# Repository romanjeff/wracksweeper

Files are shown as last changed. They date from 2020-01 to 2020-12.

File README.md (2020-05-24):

We are a Capstone team working with the Portland State University NEAR lab, under advisement by Dr. Martin
Siderius, and this repo is for the necessary files to implement or reference tha customizations we have done
to the AUV owned by the NEAR lab for academic research purposes. 

Our AUV is a Riptide Systems MP1 Mk.II, managed by a Beaglebone Black running MOOS-IvP (http://www.moos-ivp.org).

The project goal is to have full side-scan sonar capabilities, an emergency asset recovery tracking beacon, 
rechargeable power supply, and long-range wireless communications allowing us to check on the AUV's status,
give it new mission parameters, or toggle sonar functions without recovery and relaunch. Added features are
modular and removable to restore original state to the AUV.

Our sonar system is an Imagenex OEM side-scan module, and our wireless communications are done over LoRa at 
915 MHz using the Adafruit Feather M0 with HopeRF RFM95 transceiver modules. 

This project has been conducted at Portland State University by a team consisting of:

Drew Wendebrn, Matthew Moore, Patrick Hawn - Mechanical Engineering.  

Roman Minko, Adel Alkharraz - Sonar Interface Software.  

Colton Bruce - Beacon and RF link characterization.  

Jeff Roman - Communications Software.  

Jens Evens, Grace Semerdjian - Power System.  

http://www.wracksweeper.com

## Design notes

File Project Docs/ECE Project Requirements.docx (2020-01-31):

Wracksweeper: Project Design Specification

Capstone Team 3, Integrating A Side Scan Sonar System Into An AUV

Industry Sponsor: Maritime Archaeological Society

Faculty Adviser: Dr. Martin Siderius

Background:

The Maritime Archaeological Society (MAS) is searching for a Spanish galleon, the Santo Christo de Burgos, which wrecked on the Oregon coast in 1693. Hundreds of artifacts including porcelain, beeswax, and teak timbers have been found on a section of shoreline. Over the past 10 years, MAS has been conducting sonar, magnetometer and diving searches for the wreck. The searches have been severely limited due to difficult ocean surface conditions in the search area. The small boats used for the surveys and dives must launch at very precise tide levels to access the site which is a 45 minute boat ride away. Once on site, rough seas and submerged rocks make the operations difficult and potentially dangerous to the crew.

Problem:

How can we conduct long duration side scan sonar surveys without tide limitations and without putting human crewmembers in potential danger?

Objective:

To facilitate the Maritime Archaeological Society’s search for the remains, it is necessary to outfit an unmanned underwater vehicle (UUV) owned by Portland State University’s NEAR lab with side-scan sonar, a rechargeable battery solution able to support at least 8 hours continuous operation, and sufficient (at least one) emergency location systems that a recovery team can track and rescue the vehicle in the event of mission failure. While the current mission is helping the Maritime Archeological Society, all upgrades to the system will be funded by the NEAR lab and the upgrades will benefit them for future research conducted with the UUV. To do this, a multi-disciplinary team consisting of Mechanical, Electrical, and Computer Engineers must specify and implement these systems. This principal objective can be subdivided into distinct subsystems which successfully achieved will in total comprise a successful solution: emergency location systems, side-scan sonar systems, power systems, and logistics systems. If the additional engineering resources exist, an additional wireless communications subsystem may be added to this roadmap.

Constraints:

For this project, all functions must be integrated onto the NEAR lab’s Riptide Systems UUV. New features must not in any way compromise the existing functionality of the UUV and must be removable to restore the UUV to its initial state. Payload components must fit within a bay 25.5” long with an internal diameter of 6.375”. The budgetary constraint is roughly $10,000, with changes to this conditional to the research value that can be added to the NEAR lab’s resources. Based on budget and project needs, we must design this system to use the already-purchased Imagenex OEM Ethernet Sidescan Sonar PCB kit, which expects sonar images to be obtained as .872 files using the Imagenex proprietary Windows-based software. This sonar system will require a computer capable of running that software, ethernet communication with the sonar, and a source capable of providing up to 2.5W power at between 22 and 33 VDC. Sonar imaging capabilities will be constrained by those of the Imagenex product, which allows imaging range scales from 10m to 200m and can provide transducer beam widths as narrow as 0.7 ° x30 ° at 800 kHz and as wide as 2.2 ° x75 ° at 260 kHz.

Requirements:

We have identified three tiers of project requirements; the must category is the minimum viable product necessary to achieve the basic objective, while the should category describes improvements which could benefit this specific project in a meaningful way and the may category describes features which allow the work of this project to be extensible to future research purposes. Though the objective is ultimately to find the shipwreck, a successful capstone completion does not require this; the successful additions of the necessary functionality to the UUV to enable finding the shipwreck shall be sufficient.

Emergency Location Services:

- We must integrate at least one functioning emergency beacon for locating the vehicle with sufficient location resolution to be tracked within 20m anywhere within 3km of shore.
- The emergency beacon should operate regardless of whether the UUV’s piloting computer is operational and remain always-on during any deployment situation.
- The emergency beacon may broadcast to worldwide networks, an FCC-regulated amateur radio band, or to marine specific tracking networks.
- We may install an acoustic transducer for underwater chirps to have extra redundancy for the emergency locator functions.

Side-Scan Sonar:

- We must implement functioning sidescan sonar capabilities onto the provided vehicle, with data preserved in a manner conducive to image analysis and exact location discovery.
- We must provide the means to correlate sonar imaging to geographic location based on predicted GPS coordinates.
- We must provide a payload computer capable of controlling the sonar hardware either through the provided Windows-based software or code of our creation.
- We must furnish the sonar system with enough memory to store full missions at the maximum (10m image distance) rate of 265MB/hr of data collection, meaning a minimum of at least 3GB dedicated memory just for sonar data to store one mission and account a memory guardband.
- The memory device should be one which is resistant to turbulence and motion-induced write or read errors, such as a solid state drive or USB flash drive.
- We should have enough available memory for at least 10 missions to reduce the need to clear memory before each deployment.

Logistics/Power:

- We must achieve consistently predictable mission behavior and a general piloting guideline for the vehicle, which has not yet been exhaustively tested by the NEAR lab. This will be manifested as design documentation and operating manual for all integrated components.
- We must implement a battery solution for the emergency location system(s) with at least one month of standby time.
- We must implement a rechargeable battery solution with at least 1400 Watt-hours (the nominal value of the current C-cell alkaline battery pack).
- The battery pack should offer enough power for at least 8 hours’ system operation at full system load.
- The battery pack must have a charging mechanism capable of charging the full pack in less than 24 hours.
- The battery pack must be rated to at least 200 full charge/discharge cycles.
- The charging mechanism should be current and voltage-adjustable.
- The charging mechanism may have a quick-charge feature at higher current supply.
- We may implement the new features in a way that all created deliverables are easily swappable onto the NEAR lab’s other UUV, which is a smaller vessel.

Optional Communications Subsystem:

- We may implement a wireless communications solution on the vehicle capable of longer-distance mission updates than the WiFi communications already onboard, for location requests and/or remote updates to mission parameters from distances greater than 75 feet. .
- We may implement this system with sufficiently high datarate to allow remote download of sonar files without AUV recovery for redeployment after image review.

Project Requirements Capstone Team 3 Rev 2, 1/8/19 Authors: Roman, Semerjian

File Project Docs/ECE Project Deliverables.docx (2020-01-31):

Wracksweeper: ECE Subteam Milestones and Deliverables

Capstone Team 3, AUV

Sponsor: Maritime Archaeological Society

Adviser: Dr. Martin Siderius

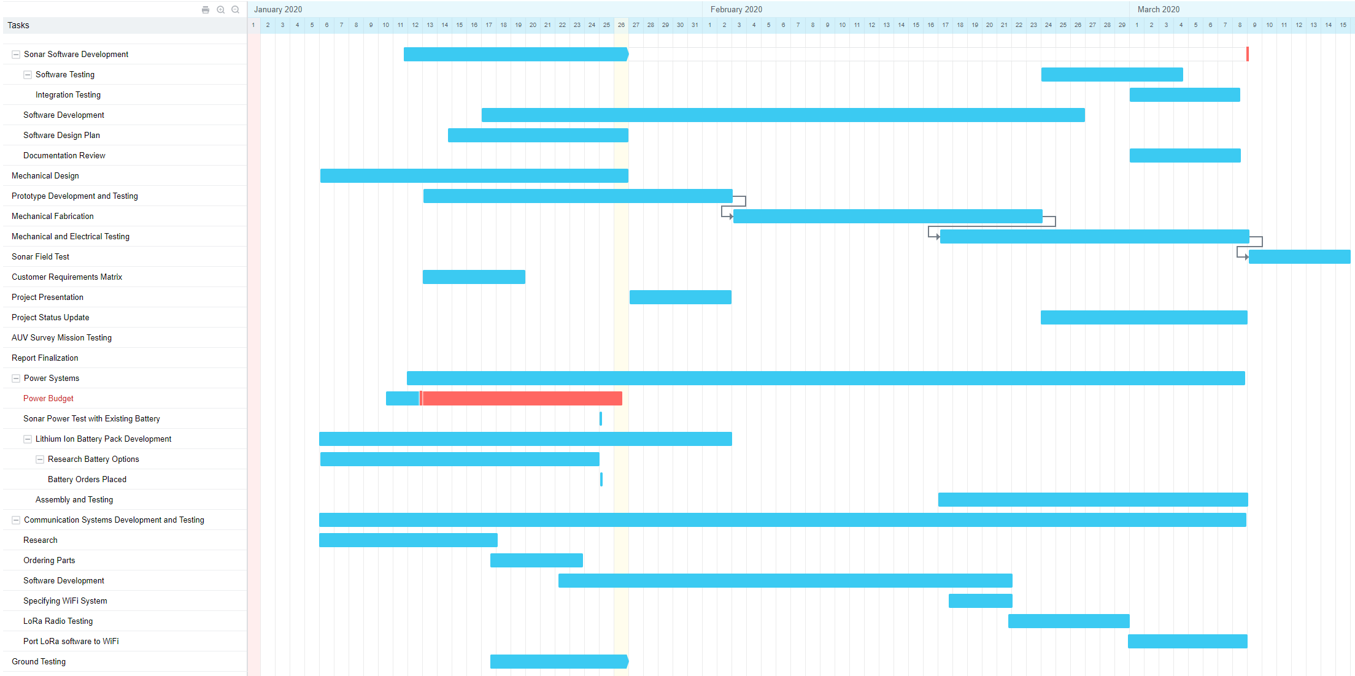
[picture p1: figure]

Figure 1: Gantt chart for the Spring term portion of the project

Key Milestones

I. Create product design specification.
II. Build project schedule.
III. Present project proposal to industry sponsor
IV. Present final project to industry sponsor and faculty adviser
V. Specification milestones:
  A. Specify power module hardware
  B. Specify sonar integration software
  C. Specify emergency location services hardware
  D. Specify remote communications hardware
VI. Modular Test Milestones
  A. Successfully test power system
  B. Successful hardware integration of power system
  C. Successfully test sonar hardware
  D. Successfully test sonar software
  E. Successful hardware integration of sonar
  F. Successfully test emergency location hardware
  G. Successful hardware integration of emergency location
  H. Successfully test remote communications hardware
  I. Successfully test remote communications software
  J. Successful hardware integration of remote communications
VII. Integration Milestones
  A. Successful systems integration test (done on dry land)
    1. Create and store sonar images physically onto IC
    2. Get location from beacon
    3. Request and receive location from AUV using wireless communications, possibly update MOOS mission and/or retrieve sonar image data
    4. Recharge battery
VIII. Performance Test Milestones
A. Characterize battery life
  a. Characterize voltage regulation and boost voltage
B. Characterize sonar performance.
C. Characterize location accuracy of emergency locations hardware
D. Characterize remote communications datarate and range.
E. Successful test mission demonstrating full system operation in water
  a. Potentially: ocean-based demonstration mission to characterize ocean performance of system

Key Deliverables

I. Product Design Specification
II. Project Schedule
III. Software to run sidescan sonar on Linux-based computer
IV. Software to allow remote user control of MOOS and possibly sonar using wireless communications.
V. AUV new features
  A. Side-scan sonar
  B. Rechargeable Battery System
  C. Asset tracking system
  D. Wireless communications system
VI. Documentation
  A. Software documented sufficiently to allow new users to install, use, and possibly adapt any code
  B. “Piloting” guide to AUV to simplify the process of generating mission parameters for MOOS-IvP
  C. Written report describing full scope of project including data
  D. Datasheets for all added components.
  E. Full revision history of all code
  F. Recorded minutes from weekly meetings documenting project progress over time.
  G. System block diagram that details the full system and differentiates between legacy hardware and new additions done by the capstone team

ECE Project Milestones and Deliverables Capstone Team 3 Rev 1, 1/29/19 Authors: Roman, Wendeborn, Semerjian

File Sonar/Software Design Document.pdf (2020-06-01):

Software Design Document | Wracksweeper (Capstone Team
3)
Version 1.1 (1/31/2020) | Authors: Roman Minko, Adel Alkharraz

Software Requirements:
Must:
- Have communication between the payload computer and the sonar board through ethernet.
- Keep writing data at every ping to the .872 file and return the file.
- Allow the sonar board to accept up to 27 bytes of switch data from the payload computer.
- Be able to start/stop recording data from MOOS.
- Be able to communicate data from the payload computer to the main computer through USB to Ethernet through a dongle.
Should:
- Implement GPS/NAV MOOS variables in the .872 file.
- Have an on/off status to MOOS whether or not the sonar system is on or off.
- Control the inputs of range, mode/frequency, gain, and balance gain.
May:
- Implement the altimeter MOOS variable in the .872 file.
- Create a script to run the program at a certain depth and stop running the program at a certain depth.

Technology Needed:
Language:
- C++
Framework:
- MOOS IVP
Network:
- TCP/IP
Source Control:
- Github

Version 1.1 (1/31/2020) | Authors: Roman Minko, Adel Alkharraz

Program Algorithm:
1. Program socket clients and check ethernet connection between the sonar board and the payload computer.
2. Create an empty .872 file that will generate data to be stored for each ping.
3. Create an array of strings that will store 27 bytes of switch data and will be passed from the PC to the sonar system.
4. Set up USB to Ethernet communication protocol between both computers.
5. Set fixed values for array:
- Byte 0 (Switch Data Header) = 0xFE
- Byte 1 (Switch Data Header) = 0x44
- Byte 2 (Reserved) = 0x00
- Bytes 4-6 (Reserved) = 0x00
- Bytes 9-17 (Reserved) = 0x00
- Byte 18 (TCP Packet Number) = 0x00 or 0x02 (will be switching on every ping)
- Bytes 19-25 (Reserved) = 0x00
- Byte 26 (Termination Byte) = 0xFD
6. Set values input from user for array:
- Byte 3 (Range) = 0x0A - 0x32 (10-50)
- Byte 7 (Frequency) = 0 - 2
- Byte 8 (Start Gain) = 0 - 40dB
7. Create a ping function that will write data to the .872 and then append that data for every new ping.
8. Receive GPS data from the pNAV application and write to the .872 file while each ping data is being processed.

Version 1.1 (1/31/2020) | Authors: Roman Minko, Adel Alkharraz

Data Flow Diagram:

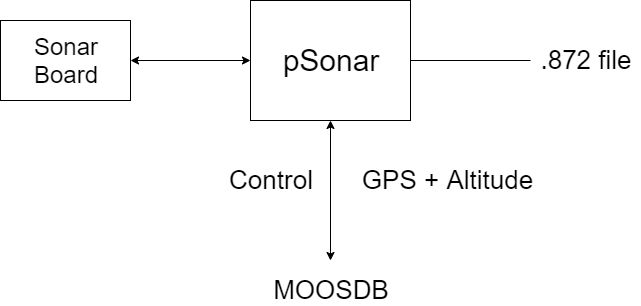
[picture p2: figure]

Hardware Diagram:

Version 1.1 (1/31/2020) | Authors: Roman Minko, Adel Alkharraz

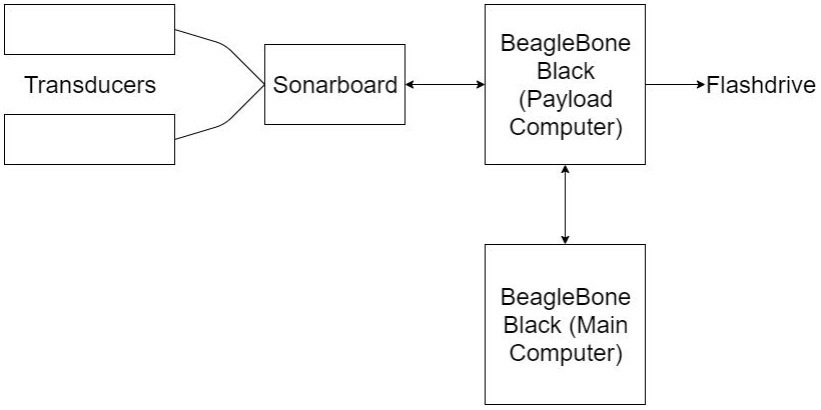
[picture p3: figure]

.872 File Reference:

Imagenex Technology Corp. "DATA STORAGE FILE FORMAT (.872)." MODEL 872 SIDESCAN (YellowFin), 1.01, Imagenex Technology, pp. 54-57. Google Drive, drive.google.com/open?id=0B4CkagcY3pD7Zmx1dFVTdnBydmdYejBQb2ZEUW5pRE tudVBR.

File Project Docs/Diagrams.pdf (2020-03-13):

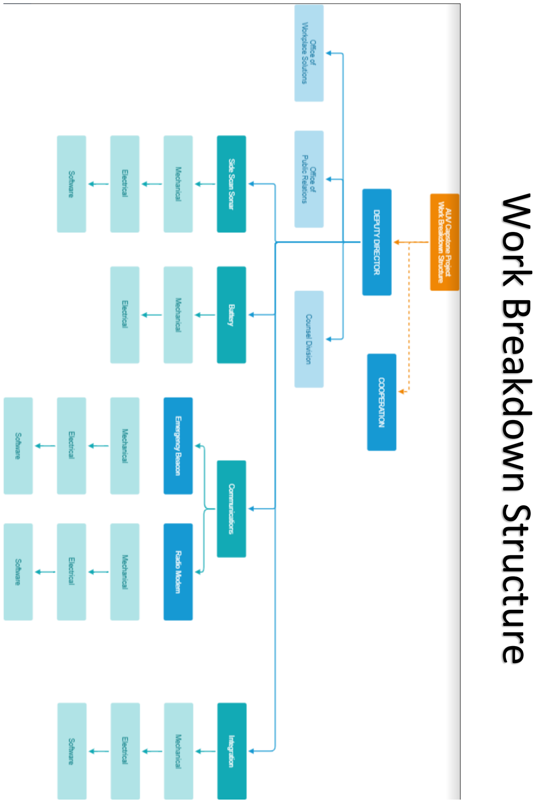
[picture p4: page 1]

Work Breakdown Structure

System Block Diagram

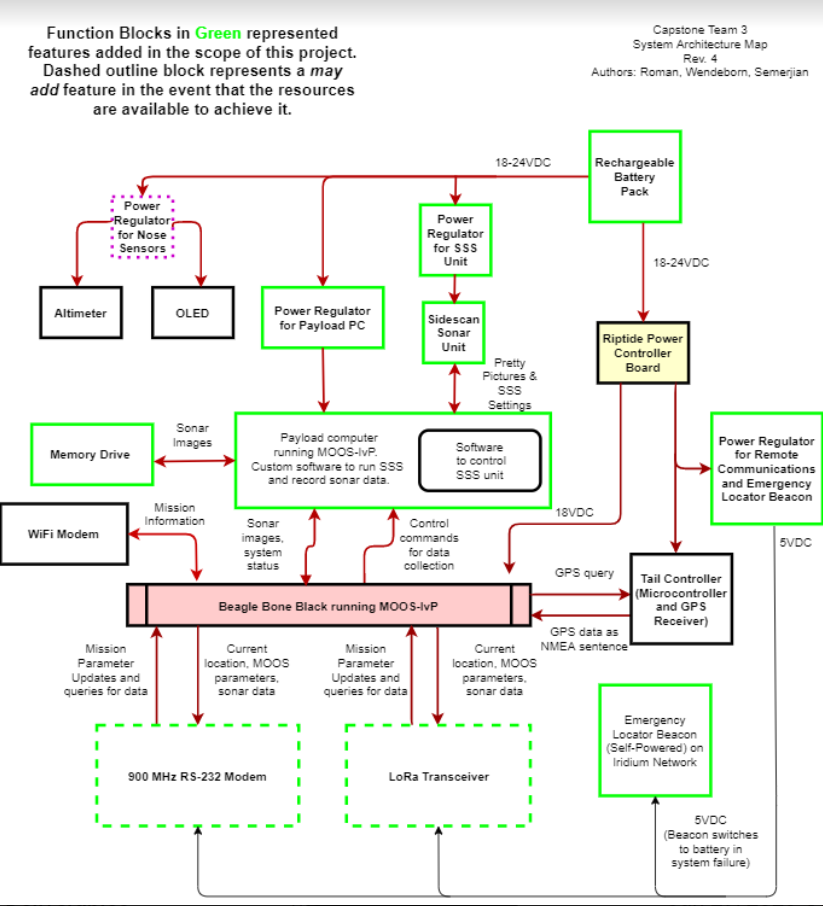
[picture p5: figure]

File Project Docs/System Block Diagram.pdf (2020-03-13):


Work Breakdown Structure

System Block Diagram


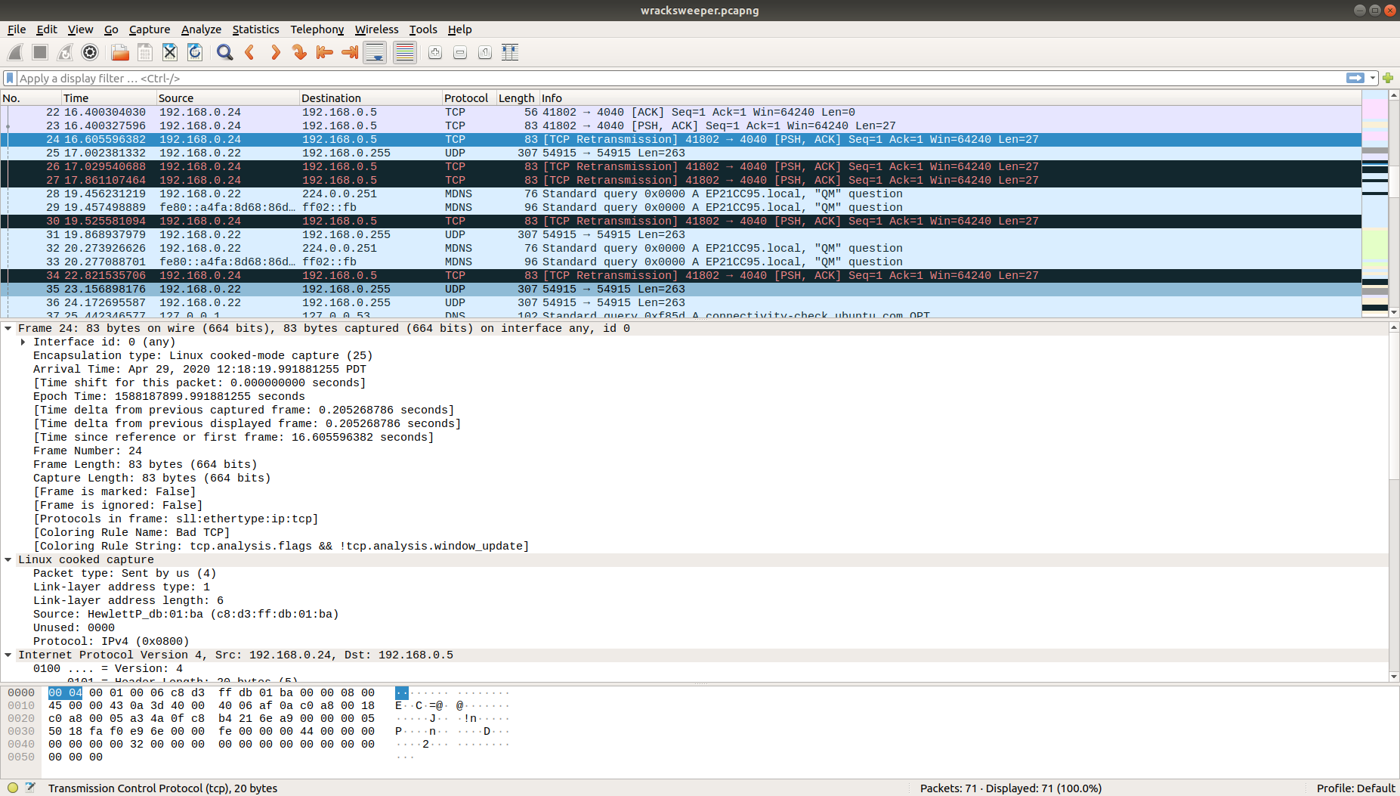
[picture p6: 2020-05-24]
Sonar/wireshark/Linux Packet Capture.png

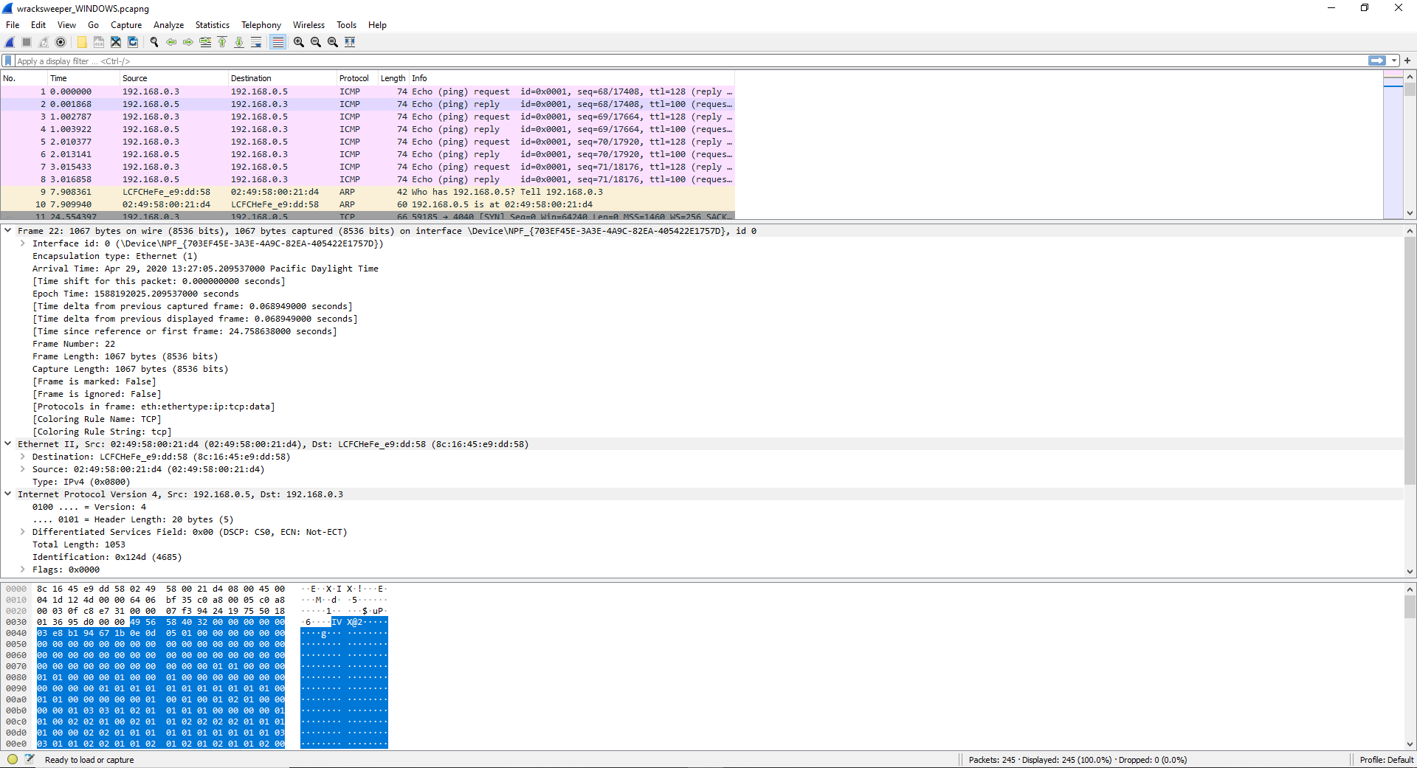
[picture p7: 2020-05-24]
Sonar/wireshark/Windows Packet Capture.PNG

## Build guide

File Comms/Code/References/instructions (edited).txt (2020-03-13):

pip3 install RPi.GPIO
pip3 install spidev
pip3 install pyLoRa
sudo apt-get install python-rpi.gpio python3-rpi.gpio
sudo apt-get install python-spidev python3-spidev
sudo apt-get install git
sudo git clone https://github.com/rpsreal/pySX127x
sudo apt autoremove

Pinout
********************************
MOSI	GPIO 10
MISO	GPIO 9
SCLK	GPIO 11 
CS	GPIO 7
DIO0	GPIO 4
DIO1	GPIO 17
DIO2	GPIO 18
DIO3	GPIO 27
RST	GPIO 22
*LED	GPIO 13	(not actually being used)
********************************
++++++++++++++++++++++++++++++++++++++++++++++++++++++++++++++++++++++++++++
To find IP address for SSH:
open command line (Ctrl+Alt+t)
type in ifconfig

for WIFI:
	look at wlan0:
			inet 192.168.xx.xxx	<-- this is the ip for ssh
for Ethernet:
	look at eth0:
			inet 192.168.xx.xxx	<-- this is the ip for ssh
++++++++++++++++++++++++++++++++++++++++++++++++++++++++++++++++++++++++++++
----------------------------------------------------------------------------
To run a single easy command to SM sensor:
	-open command line (Ctrl+Alt+t)
	-cd to:
		Desktop/AirSciences/SMsensor/
	 or
		home/pi/
		(by default should be here when you open command line)
	-type command: make bang
To run a specific command to specific device:
	-open command line (Ctrl+Alt+t)
	-type command: python3 /home/pi/Desktop/AirSciences/SMsensor/LORA_PI_TX.py [SensorName]
		e.g.   python3 /home/pi/Desktop/AirSciences/SMsensor/LORA_PI_TX.py SM01

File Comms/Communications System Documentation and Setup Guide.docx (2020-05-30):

Guide to Setup and Use the WAVES Wireless Communication Subsystem

Installing and Configuring the Adafruit Feather M0 with LoRa

Both the AUV and shore controller radios use the same Arduino sketch, and both will need u.FL connectors for their antennas soldered to them in the appropriate footprint. The radio to be used in the AUV will additionally need two 2.2k resistors soldered directly: one from pin USB to A2, and one from A2 to GND. There will also be wires from GND, Tx1 and Rx0 to the Beaglebone black that need soldering. Please consult the full system wiring diagram to ensure this is correctly executed, as inverted UART connections will lead to nonfunctional communications.

(This is essentially a summary of the instructions available from Adafruit here: https://learn.adafruit.com/adafruit-feather-m0-radio-with-lora-radio-module/setup)

In order to program the Adafruit Feather M0 using the Arduino IDE, one first needs the Arduino IDE. Once the most updated version is installed, go to File->Preferences and add to the “Additional Boards Manager URL” this address:

https://adafruit.github.io/arduino-board-index/package_adafruit_index.json

If other URLs are already listed, simply add a comma and then the above (as with PATH additions).

Next, go to Tools->Boards->Board Manager and select from the “Source” dropdown menu the “Contributed” section and install the “Adafruit SAMD Boards” and “Adafruit AVR Boards” and “Arduino Leonardo and Micro MIDI-USB” libraries. Make sure to FIRST install any Arduino Boards library which has inclusions for the Feather (Arduino SAMD and Arduino AVR). Restart the IDE, then plug in the Feather M0 and verify that the Tools->Ports Menu shows “COMxx: Adafruit Feather M0” for xx whichever USB port you are plugged into. Select the correct board from Tools->Boards. Now, you can install a sketch onto the Feather! There is a sample Tx sketch and a sample Rx sketch on the Adafruit guide above which can be monitored from the Arduino serial monitor to verify that the two boards are pinging each other. DO NOT TRY TO USE THE RADIOS WITHOUT ANTENNAS. Either use a 13cm wire or your intended antenna.

The first lines of code below the library imports on the AUV_Comms Arduino sketch allow the toggling of modes. The appropriate version of the sketch is obtained by compiling and uploading after ensuring the proper toggles are either uncommented or left commented out. A guide to these possible settings is as follows:

#define SHORE_CLIENT | #define DEBUG | USE CASE

commented | commented | Official AUV installation with BBB. All arduino interaction will be over UART with no extra information or added UX dialogue. Validate both radios operational with DEBUG modes and USB terminal before switching to this setting.
uncommented | commented | Not a useful state. Avoid.
commented | uncommented | Troubleshooting AUV radio via USB with similar terminal interface as used for Shore controller radio.
uncommented | uncommented | Official shore controller radio setting. Use with USB serial interface.

Available Radio Methods:

The serial input is fairly reliable and allows backspace, so it should be fairly easy to interact with. Whatever you type will, as long as the transmission executes properly and is received and acknowledged, be relayed verbatim to the AUV Beaglebone Black from the perspective of root kernel access. This link is not suitable for interactive programs or lengthy output, and not all command line operations will behave predictably, but most may be performed by preceding your command with “sudo sh -c” to spawn a child shell from which to execute your desired operation.

The following special commands do not result in AUV interaction but govern various available radio options:

“-changemode bw500cr45 sf128” gives the syntax form for a coordinated and handshaked settings change on both radios. All settings options must be specified, with the options listed and explaiend in the next section.

“-changeme bw500cr45 sf128” allows a local-only settings change. In the event that the shore radio loses power or is reset, the same settings can be implemented to regain the link, but there is user responsibility to remember the settings they were using. Once a preferred setting is found for a specific mission’s operating territory and link conditions, it is recommended to recompile and reupload the sketches with those settings as default.

“-verb” gives verbose output to monitor link conditions, appends all received messages with total packet time from sending to receiving acknowledgement and the SNR and RSSI detected. If packet times far exceed those expected for the settings in use, it may be assumed that some retries were necessary.

“-memmon” can be used in sketch modification to check memory use over time when new features are added. If the new features cause memory leak, this may be determined by invoking this method and observing memory use changes over the course of an interaction section.

“PING” is a simple ping to test that 2-way communication is working without any AUV interactions. The response comes from the Arduino, not the BBB, and it can be convenient to check the link by turning -verb on before a ping, then turning -verb back off.

Choosing Radio Settings

The “Different LoRa Settings” Spreadsheet gives a rough guide to the datarate differences between the different available settings. Here are the meanings of those settings.

We have provided access to three of the available chirp bandwidths: 125kHz, 250kHz, and 500kHz. The smallest bandwidth is thought to offer roughly 6dB improvement in link budget (theoretically a doubling of range) but with proportionally longer packet time, about 4x greater on-air time in tests.

The coding rate sets the Hamming Code depth, from 4/5 to 4/8. The 4/5 setting only enables a single parity bit, while the 4/8 setting can detect multiple bit error locations. This setting is exclusively related to reliability and does not affect link budget, but on-air time increases slightly. This option is somewhat redundant due to the reliable datagram’s CRC and so it will not dramatically improve performance nor will it significantly hurt on-air time. It is recommended to leave at 4/5 except in specific instances.

The spreading factor specifies chips/symbol, where symbol rate is set by adjusting the number of phase changes (chips) used for each symbol. A high spreading factor results in greater on-air time but improved detection and decoding. Each increase in spreading factor doubles the on-air time but can potentially provide around 2dB improvement in link budget. The available spreading factor options are 128,256,512,1024,2048,and 4096. It is recommended to limit spreading factor to 2048 at most, as 4096 can lead to packet times up to 8s and it is likely that they will time out. The timeout setting can be adjusted in the sketch, but failed packets at faster datarate are also subject to it.

Current Default settings in the sketch:

BW: 500

CR: 4/5

SF: 256

# RETRIES: 3

TIMEOUT: 4 seconds

Each retry attempt is given the full timeout period if no acknowledge is received. This means packet failure can be detected for certain within 16 seconds of initial transmission.

Recommended default settings for poor link environments:

BW: 500

CR: 4/5

SF: 2048-4096

Estimated Packet time: 0.7-1.2s

Since the AUV is floating, it is as likely that the RF link is broken mid-packet as not and so the lowest possible spreading factor will yield best performance due to the low on-air time. However, physical link budget is 6dB worse at the higher bandwidth, which makes it something of a runoff between the following set of settings as far as possible range is concerned.

BW: 125

CR: 4/5

SF: 512 - 2048

Estimated packet time: 0.8-2.7s

Installing the Communications Software on the Beaglebone Black

1. (If starting with new Beaglebone Black) :

Flash a Debian 9.5 or earlier image onto BBB:

Create uuuv user with “sudo adduser uuuv” then make a superuser with “sudo usermod -aG sudo uuuv”. Check that it worked by “su -uuuv” then run “sudo whoami” and make sure root shows up. Unzip riptide installer package to some directory, then run ras-uuuv-dashboard-psreinstall.sh and finally install.sh, selecting 1MP, Mk. 2, Sparton IMU as the install options.

2. Log in, then:

sudo nano /etc/network/interfaces

Append to end of doc:

iface usb0 inet static

address 192.168.7.2

netmask 255.255.255.252

network 192.168.7.0

gateway 192.168.7.1

dns-nameservers 8.8.8.8

post-up route add default gw 192.168.7.1

In terminal again:

sudo reboot

Share your internet connection from “networks and sharing” in your OS, then ssh into the BBB which should now be internet-enabled to get more software up on that thing.

Once rebooted:

sudo ntpdate pool.ntp.org

sudo apt-get update

sudo apt-get install minicom build-essential python-dev python-pip -y

sudo apt-get install watchdog

sudo apt-get install python-systemd

sudo pip install Adafruit_BBIO

sudo pip install pyserial

NOTE: depending on the default python, it may be necessary to change the systemd unit file to direct the process to be run from /usr/bin/python3 or /usr/bin/python2.7 test the script by running it on demand instead of as a service before enabling it in systemctl.

In /home/debian, place the pyTerminal.py file.

Scp ./pyTerminal.py debian@192.168.7.2:/home/debian

In /etc/systemd/system/ place the pyTerminal_service.service file. You will need to either scp as root or temporarily place it as a user then move it with sudo privilege.

In /etc/systemd/system.conf uncomment the lines relating to watchdog timers and change the RuntimeWatchdog to 15 seconds.

Then from the command line, verify that systemctl can find the unit file with:

$ systemctl list-unit-files | grep pyTerminal_service

And see the output:

pyTerminal_service.service disabled

Finally: release it to control of systemctl

sudo systemctl enable pyTerminal_service

Sudo systemctl daemon-reload

Sudo systemctl start pyTerminal_service

Check that it started and reported running correctly

Sudo systemctl status pyTerminal_service

BEFORE ENABLING AS SERVICE:

Run as simple python script with comm system connected and verify that some commands work correctly. Try an ls, etc. It is possible that some debugging and troubleshooting will be required to implement this if your kernel and/or python installations deviate from the dev system. Sorry about that.

IMPORTANT: OTHER WARNINGS

Some commands may not work correctly since the service runs from the kernel (not a shell). If shell code is essential, must try “sudo sh -c” before the command to spawn a child process shell to run it from.

Because Lora is not full-duplex, any process output initiated over LoRa will try to continue to send until complete. It is the responsibility of the user to prevent the system from trying to send long files or entering processes requiring interactivity. Due to the way commands are directed as a subprocess, it is likely that the usual means of suppressing “full” output like grep and and tail will not work. Full exploration of the capabilities are recommended before attempting anything but simple file IO.

The Most Important Outstanding Unfinished Tasks:

As it is, the correct commands to toggle the sonar on with the correct settings need to be found. The script itself is locally called on the payload computer by running “/home/wracksweeper/waves.sh” but addressing the payload computer correctly at the AUV’s ethernet port and sending this command has not been successfully accomplished due to time limitations.

Additionally, the correct command line instructions are needed by which a GPS current nav-data structure can be stored as a file, then parsed and built into a convenient single line for transmission and/or storage on the Arduino as a “last known coordinates” setting. It is believed that the uXMS feature of MOOS must be exploited for this, or perhaps a custom AppCast set up. Once this is done, the Arduino sketch and the pyTerminal service must both be modified to allow for regular transfer of last-known GPS data to the Arduino so it’s available on demand.

Improvements that need making:

Run the terminal service from uuuv instead of root. This will require access to the uuuv or an identical virtual machine to verify correct operation.

There is a scheme by which “esc” can be sent which will terminate output, but the messages never arrive send both radios are sending and neither is listening. Instead, a timeout may be implemented that prevents outputs with longer than 30s of data unless a keyword is included at the head of the command. The “esc” function may be possible by use of the waitCAD() or isChannelActive() class members, but early attempts to implement these methods were not successful.

The reliable datagrams can also be made secure and encrypted by invoking the RHEncryptedDriver class. This should be considered high priority due to the nature of the RF link, but as it represents nontrivial change to the functionality of the current software and requires additional crypto libraries it must also be assessed for its effects on system performance and it will only be a recommendation for future work. https://www.airspayce.com/mikem/arduino/RadioHead/classRHEncryptedDriver.html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

High priority for future work on this system would entail the creation of a terminal emulator GUI which offers a command line but also buttons and pulldown menus to access the “known safe” common features and the option to export received data to a local MOOS instance for mapping either once or continuously. Logging and interpretation scripts would also be extremely useful. A means of generating MOOS mission update requests that are callable with a single command line entry would extend the level of overall control significantly, as would a method of algorithmically reviewing sonar data and isolating potential points of interest to be able to report to shore if anything worth looking at was found. Machine vision techniques are likely required for this, but the payload BBB offers the available compute power without additional hardware overrhead.

Other future-facing improvements: Additionally, a backup GPS device may be installed which is slave only to the MCU regulating wireless communications, offering redundant asset tracking which can be correlated against beacon data if system failure occurs and MOOS offers the API to facilitate joystick-based piloting, which could be easily added to the existing hardware and improve the launch and recovery process significantly. The MCU governing communications could also be exploited to incorporate leak detection sensing and engage some method of emergency protocol for the AUV.

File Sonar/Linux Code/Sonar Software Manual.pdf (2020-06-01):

Sonar Software Manual | Wracksweeper (Capstone Team 3)
Version 1.0 (5/31/2020) | Author: Roman Minko
Accessing the BeagleBone Black using SSH
1. Connect the BeagleBone Black to your computer with the USB-A (your computer) to Mini-USB (BBB) cable
2. SSH into the BeagleBone Black
- Windows User
i. Install the SSH client Putty on your computer if you don’t have it already
ii. Open up Putty and enter “192.168.7.2” as the Host Name and 22 as the Port #
iii. Select the connection type as “SSH” and click “Open”
iv. If you encounter a security alert, click “Yes” and continue (after the
| server’s host key is cached in your registry, you won’t have the
alert pop up anymore)

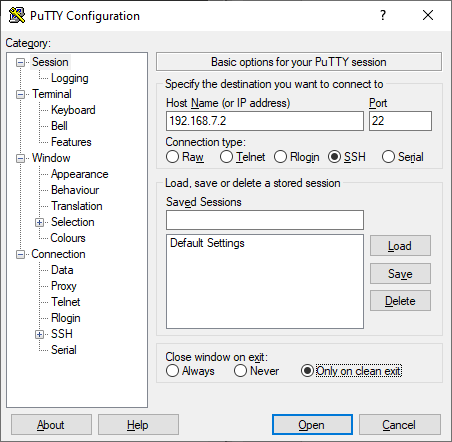
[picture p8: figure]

Figure 1: Your configuration should look something like this
v. Login as: wracksweeper
Password: wracksweeper
- Linux User
i. Open up a terminal window (CTRL + ALT + T)

ii. Type in the command: “ssh wracksweeper@192.168.6.2” iii. Enter the password: wracksweeper

Note: Once you’re in, the remaining steps will be the same for both Windows and Linux users

Overview of Everything on the Payload BeagleBone Black

If you do an “ls” to list your current directories contents, you’ll notice a directory “wracksweeper” and a file “waves”

- wracksweeper directory – contains the source code, header files, Makefile, and README
- waves script – shell script to run the software

You can find the directory where the SD card is mounted on in “/media/Data”

In order to confirm that the SD card is mounted in that directory, type “df” t show file system disk space usage and look for the filesystem that is around 64GB (SD card storage) and you should be able to see that it’s mounted on “media/Data”

In that directory, there is a folder called “missions”, which is where all of the mission (.872) files will be stored

WARNING: Make sure that the sonar board is connected to the BeagleBone Black via ethernet and that the transducers are connected to their respective ports on the sonar board, otherwise the program will run, but no mission file will be created.

Running the Sonar Software on the Payload BeagleBone Black

Due to only having single line command access for now on, the software is ran through a shell script that takes in arguments for the filename and different parameters

1. Change to the default directory, if you’re not already there, by typing “cd”
2. Run the script with this syntax:
./waves <filename> <range> <frequency> <start gain>

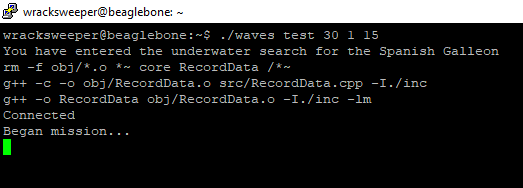
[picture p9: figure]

Figure 2: Example execution of sonar software
3. We currently don’t have a clean way of stopping the software, so in order to stop recording, you’ll need to perform a CTRL + D to stop running the program
4. Your recorded mission file will be stored on the SD card located in the “/media/Data/missions” directory

Future Improvements

In the GitHub repository, I pushed another folder containing future Linux code that has partially implemented ncurses to use a keypress as a command to stop recording. Using ncurses is not the most ideal way of implementing this, so I suggest using multithreading to have two processes running at the same time. The function “getch()” is the easiest to use, but the problem with it is that it waits for a user input, so it’s not ideal if we’re recording data at the same time while waiting for a user input. That’s why we tried ncurses since it allows you to use “getch()” without waiting for a user input and still recording data at the same time.

Another minor improvement is when you’ll have access to more than just single command line access, prompt the user for inputs on the filename and the parameters.

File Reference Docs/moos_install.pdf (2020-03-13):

# The MOOS-IvP Build System

Christian Convey (christian.convey@navy.mil)

2007-08-14

Abstract

This document details the design and intended use of MOOS-IvP’s build system.

## Contents

1 HOWTO Build MOOS-IvP | 2
1.3.2 | Required Steps for CMake-based build (Easy Technique) . | 12
1.3.3 | Required Steps for CMake-based build (Advanced Tech-
2 MOOS-IvP Build System Implementation Details | 15

1

3 Future Work | 15

## 1 HOWTO Build MOOS-IvP

This section gives some basic background in using any CMake-based build system, and then explains how to use MOOS-IvP’s particular build system.

### 1.1 CMake

### 1.1.1 Overview

This section gives a brief overview of CMake, but clearer and more complete sources of information exist:

- The project’s website: cmake.org
- Mastering CMake, by Ken Martin and Bill Hoffman.
- The CMake users email list: cmake@cmake.org. You can sign up for this at the cmake.org website.

CMake (cmake.org) is a cross-platform build system. Compared to traditional Makefiles, CMake’s control files (named CMakeLists.txt) tend to be much shorter and easier to read.

CMake has a number of back-ends for various operating systems and Make programs (gmake, nmake, etc.) and IDEs (MS VisualStudio, KDevelop, Apple’s XCode, etc.) CMake-based build systems trivially support some features that can be a real hassle to implement in hand-written Makefiles, such as calculating header file dependencies and supporting an install target.

The cmake program reads in a project’s CMakeLists.txt files and produces one or more files suitable for use in your build-system of choice (GNU Make, MS VisualStudio, etc.) These generated build files will typically invoke the cmake program when building certain targets; therefore CMake must be installed on any computer that will execute cmake-produced build files.

2

### 1.1.2 Language for Describing Makefiles

CMakeLists.txt files are written in an imperative language which is documented on CMake’s website. The language lets you set variables and supports branching, looping, and a limited form of subroutines (called MACRO’s).

When cmake processes a project’s CMakeLists.txt files, the program embodied in those files specifies the details of the build system to be created. The CMakeLists.txt files execute sequentially, specifying details as they run. Then end product is not a fully built version of your project, but rather a set of build files (Makefile, etc.) that when executed will build your project.

The sequential nature of the programming language lets variables be computed, helper programs run, conditions to be tested, etc. in order to determine what should happen when the person building the project finally runs make (or performs the equivalent action in VisualStudio, XCode, etc. ).

### 1.1.3 Federated Builds

A typical CMake-based build system will contain one CMakeLists.txt file in each of the project’s source tree’s directories. A simplified depiction of this scheme is shown in Figure 1.

The project’s top-level CMakeLists.txt file typically sets variables that govern the entire project’s build details, such as the directory into which the built libraries and / or executables should be placed after being linked, and the directory(ies) in which the project’s header files can be found.

The CMakeLists.txt files in the internal levels of the source tree often do nothing other than call ADD_SUBDIRECTORY on each of that directory’s subdirectories. (ADD_SUBDIRECTORY is very similar in effect to the C preprocessor’s #include directive.) The practice of having intermediate-level directories’ CMakeLists.txt files mostly just consist of ADD_SUBDIRECTORY is common because those directories often exist merely to group together subdirectories into units that are meaningful to the programmer. Therefore those directories have little significance to the way the project code is actually built.

The source tree’s leaf directories typically contain the bulk of the project’s interesting source code, with each subdirectory having the code for a single library or executable. The CMakeLists.txt file in one of these leaf directories will generally contain an ADD_LIBRARY or ADD_EXECUTABLE command which leads to the compilation and linking of that one particular program / library.

3

cmake-file-tree-eps-converted-to.pdf

Figure 1: Conventionally each directory in the source code tree contains a CMakeLists.txt file.

4

### 1.1.4 Inherited Variables

CMakeLists.txt scripts have variables, similar in form and purpose to make shell variables. They’re treated and manipulated as text, and lists are generally represented as a single string in which spaces separate the list’s elements. (Another convention is sometimes used in CMake’s functions, where semicolons rather than spaces separate list elements.)

In traditional Makefiles, a child make process inherits a parent make process’ variable values. A similar effect exists in a hierarchy of CMakeLists.txt files, but via a different mechanism:

Consider Figure 2. Using these CMakeLists.txt files would look like this:

cmake -f CMakeLists.txt
(... some miscellaneous output from cmake ...)
Y
X
(... some miscellaneous output from cmake ...)

Notice how the subdirectory’s file Bar/CMakeLists.txt not only inherits a value of MyVar from the parent CMakeLists.txt file, but Bar/CMakeLists.txt also affects the behavior of the parent CMakeLists.txt file. (Bar/CMakeLists.txt) modifies the value of MyVar, and that new value is in effect in the lines of the parent CMakeLists.txt file that follow the ADD_SUBDIRECTORY call.

Contrast this to behavior to a Makefile-based system where a parent directory’s Makefile calls make -f Bar/Makefile. In that scenario, there is no mechanism by which Bar/Makefile’s modifications of make variables could propagate back to the parent directory’s running instance of make.

### 1.1.5 Cache Files

Some CMake variables are computed each time you run cmake, but other cached variables, once set, have their values recorded and stored in a file named CMakeCache.txt. Variables stored in this file can be edited using the ccmake program (Linux) or
the CMakeSetup.exe program (Windows). This not only lets users enter certain data just one time (i.e., the string that specifies the version of MOOS being
built), but it also exposes some CMake variables that whose value the user might want to correct.

For example, when CMake looks for the FLTK libraries, one variable that gets set is FLTK_DIR. If CMake’s FindFLTK package can’t figure out where the FLTK libraries are, it will set the cached FLTK_DIR variable to have a value of FLTK_DIR-NOTFOUND. The user can run ccmake or CMakeSetup.exe to manually set the value of FLTK_DIR to a valid value (typically /usr/lib for that particular

5

file-structure-eps-converted-to.pdf

Figure 2: ADD SUBDIRECTORY joins CMakeLists.txt files much like C’s include

6

cmake-data-flow-eps-converted-to.pdf

Figure 3: Build-time relationship between CMake, make, and their control files

variable), and then re-run cmake. This is typically enough of a help for a CMake package such as FindFLTK package to work out the rest of the details it needs to.

Sometimes a CMakeCache.txt file will contain so many bad values that the user decides it’s better just to start from scratch. In general it’s safe for a user to manually delete a CMakeCache.txt file. When he next runs cmake, the variables whose values had been contained in the file will simply be freshly computed.

### 1.1.6 cmake, ccmake, CMakeSetup.exe

Figure 3 shows the relationship between CMake, the traditional make program, and various control files. cmake is used to generate build-system files from a set of CMakeLists.txt files. cmake will also read from and write to a CMakeCache.txt in the directory from which cmake is run.

Sometimes cmake doesn’t succeed the first time it’s run. The FLTK module from above is a good example. We can easily write CMakeLists.txt that would

7

terminate the cmake invocation if the cached FLTK_DIR variable had a value of FLTK_DIR-NOTFOUND.

One solution to such a problem would be for the user to specify a good value on the cmake command line. For example:

> cmake -DFLTK_DIR=/usr/lib -f CMakeLists.txt

This approach is sometimes the best, but ccmake and CMakeSetup.exe offer a more interactive approach to configuring the build system. Within these tools, you continue re-running cmake and modifing cached variable values until the cmake succeeds. At that point the user instructs the tool to “generate” the build system files (on Linux, this typically includes a set of Makefiles). Once this is done the user will be ready to run make (or whatever the equivalent action is for his build tool).

Note that ccmake and CMakeSetup.exe will not create the build system files until the set of CMake variable values has stabilized. This means that the tool must observe that when it runs cmake, none of the cached variables’ values have changed. This relates to the fact that run n of cmake may set new value in a cached variable, but the ramifications of that new variable aren’t fully realized until the next invocation of cmake makes use of that value.

Practically speaking the need to iteratively run cmake within ccmake and CMakeSetup.exe doesn’t feel burdensome. And if one knows the proper values for all of the CMake variables of interest, you can set them on the cmake command line as shown above, thus entirely avoiding the need to run ccmake or CMakeSetup.exe.

### 1.1.7 Finding External Packages

When it comes to telling the build system where to find the header files and development libraries for external packages such as FLTK or libGLU, CMake is similar to GNU’s autoconf: Contributors write CMake modules to discover the details needed to use a particular program, library, etc. automake packages are written in the m4 macro language, whereas CMake modules are written in CMake’s scripting language - the same language used in CMakeLists.txt files.

CMake includes a number of these packages as a part of its standard distribution. On Ubuntu Linux you can see those modules in the directory

/usr/share/cmake-2.4/Modules/

You can also write your own modules, but you need to tell CMake about which directories to search when looking for extra modules that you’ve written.

8

Sometimes the standard supplied modules are of lower quality and you might want to use your own CMake code instead. A good example is FindFLTK, which is used by both MOOS and IvP in order to discover the locations of the include files and libraries for the FLTK library. FindFLTK does a bad job of discovering the locations of these files, even if they’re in /usr/include/FL and /usr/lib, as expected. FindFLTK is also structured so that it’s inconvenient to test whether or not FLTKs header files and libraries have been found, without also requireding that the fluid program (unused by MOOS and IvP) is installed.

MOOS avoids this quality problem by using a customized version of the module, implemented in the file:

MOOS/MOOSFindFLTK.cmake

But even that customized version of FindFLTK has a painfully complex implementation, and it still needs help just to realize that it should look in the directory /usr/lib to find the FLTK libraries.

### 1.1.8 Multiple Attempts to Configure the Project

Configuring a CMake-based project is the act of attempting to create the build files (i.e., Makefile, etc.) needed to build your software. As described in Section 1.1.6, this make require multiple attempts in order to ensure that all of the important CMake variables have the values required to build your software the way you want it.

### 1.1.9 In-source vs. Out-of-source Builds

Sometimes we want to maintain multiple builds of the same software, where the builds differ by details such as debug vs. optimized build, or perhaps where files will be copied to if one were to run the command make install. (In the MOOS-IvP project, the scripts for creating the Debian package files rely on this feature.)

To support the concurrent existence of multiple kinds of builds, the binaries produced by the build process (object files, libraries, and programs) for different types of builds must reside in different directories. Even the generated Makefiles for the different build types must be separated, because (for example) the directories to which files will be copied when make install is run are stored in the Makefiles generated by CMake.

An in-source build is one where the Makefiles, object files, etc. associated with a build of the software are stored in the same directory tree as the source files themselves. An out-of-source build is one where the Makefiles generated by CMake, and the object files, libraries, and programs produced by those Makefiles, are stored in a different directory tree than that in which the source

9

code resides.

CMake can accomodate either in-source or out-of-source builds. When one creates an out-of-source build, CMake will generally create a directory tree whose structure mirrors that of the source tree, and populate that newly created directory tree with Makefiles and various extra subdirectories needed to fully build the software. When one creates an in-source build, CMake will place those same Makefiles and extra subdirectories directly into the appropriate locations within the source code’s directory tree.

When one runs cmake or ccmake or CMakeSetup.exe to initially configure a project, he passes as a command-line argument the root of the source code directory tree. CMake will look within that specified directory tree for the CMakeLists.txt files that guide the creation of the build files, but it will create the build files (Makefile, etc.) in the current working directory from which cmake was invoked. Therefore an in-source build tends to look like this:

cd ~/MyProj/src
ccmake ./
make

and an out-of-source build tends to look liks this:

mkdir ~/MyBuildDir
cd ~/MyBuildDir
ccmake ~/MyProj/src
make

It’s often preferable to use out-of-source builds when possible. When one configures a project using cmake (or ccmake or CMakeSetup.exe), certain details become fixed and cannot be changed no matter what environment variables you set prior to running make within that build tree. Examples include whether the code will be built in debug or release mode (governed by the value of the CMAKE_BUILD_TYPE variable), and where files will be installed if you run make install (governed by the value of the CMAKE_INSTALL_PREFIX variable).

If one wants to rapidly switch, for example, between release and debug builds, then it may be desirable to maintain two separate out-of-source configurations that differ only in their value of the CMAKE_BUILD_TYPE variable. One might therefore do something like this:

mkdir ~/MyBuildDir/release
cd ~/MyBuildDir/release
ccmake -DCMAKE_BUILD_TYPE=Release ~/MyProj/src make

10

mkdir ~/MyBuildDir/debug
cd ~/MyBuildDir/debug
ccmake -DCMAKE_BUILD_TYPE=Debug ~/MyProj/src
make

Another example of where the use of out-of-source configurations is useful is when the MOOS-IvP build system produces Debian packages. Our technique for producing the different Debian packages involves varying the value of the CMAKE_INSTALL_COMPONENT CMake variable. It seemed overly intrusive to reconfigure the build directory used by the person creating the Debian packages, so the Debian packaging scripts use out-of-source builds whose configurations have various values for the CMAKE_INSTALL_COMPONENT CMake variable.

In order to remain consistent with the general behavior of the of IvP’s previous build system, the top level build.sh script performs an in-source build. However, the MOOS-IvP project can be built equally well as an out-of-source build.

### 1.2 Source Tree Organization and the Two Build Systems

When targeting a Make-based build system, cmake will produce a set of files named Makefile, one in each directory of the tree.

In order to permit MOOS-IvP’s old set of Makefiles to remain present in the source tree, I renamed all of the old Makefiles to be named makefile (note the lower-case filename). In the old make system, the makefile in one directory builds the contents of its child directories by invoking the command make -f (child-dir)/makefile. Because the tweaked version of the old build system specifically calls make on the lower-case-named makefile, the two build systems manage to remain completely independent.

Our expectation is that after several months of gaining confidence in the CMake-based build system, Mike Benjamin will permit the old makefile files to be removed from the source tree.

### 1.3 Building MOOS-IvP

### 1.3.1 Required Steps for old makefile-based build

In contrast to a previous organization of the MOOS-IvP directory tree, the ivp/src no longer contains a subset of the programs and libraries that are part of the MOOS project. Therefore if one is using the old makefiles to build IvP, he must first explicitly build the MOOS libraries so that they’re available when the ivp programs are being linked. This is the primary difference between the old and new technique for building IvP when using the old-style makefiles.

11

The steps are as follows:

1. Check-out or download the moo-ivp source code, into some directory foo/.
2. Build MOOS:
2.1. cd foo/MOOS
2.2. ../build.sh
If this step fails, you may need to modify one or more of the directories mentioned in the file ../build.sh.
Note that MOOS is being built with CMake, even though these present instructions describe building IvP without using CMake. This is because (a) we’ve decided to stop importing code from the MOOS project directly into the IvP source tree, and (b) the MOOS project uses CMake rather than hand-written makefiles.
3. cd foo/ivp/src
4. make -f makefile

If you don’t specify -f makefile, and have previously used the CMake-based build system in this directory, then your invocation of make will probable use the file ivp/src/Makefile (note the upper-case M). That file is created by CMake, which presumably isn’t what you want since these present steps describe how to use IvP’s non-CMake build system.

### 1.3.2 Required Steps for CMake-based build (Easy Technique)

1. Check-out or download the moo-ivp source code, into some directory foo/.
2. cd foo/
3. ./build.sh

### 1.3.3 Required Steps for CMake-based build (Advanced Technique)

This is the approach you’ll need to take if CMake can’t find some required header file or library, or if you want to tweak what set of programs and libraries are built.

1. Check-out or download the moo-ivp source code, into some directory foo/.
2. cd foo/

12

3. ccmake -f CMakeLists.txt

Within ccmake, set variables as desired until you can generate the build files. Then generate them (within ccmake). Documentation of ccmake and CMakeSetup.exe is out of the scope of this document, but the book Mastering CMake is an excellent source of information. An explanation can also be found here:

http://www.cmake.org/HTML/RunningCMake.html

Note that the file foo/build.sh shows an invocation of cmake that sets some CMake variables that the current build system has trouble figuring out on your own. If you’re having trouble getting any of those variables to take on good value when using ccmake, consider using the respective values mentioned in foo/build.sh

4. make

### 1.3.4 Requried Ubuntu Packages

The following is a (perhaps) partial list of packages that must be installed on a Ubuntu 7.04 (“Feisty Fawn”) system in order to build IvP and the non-Matlab parts of MOOS:

Ubuntu package | Reason needed
cmake | Integral part of build system
mesa-common-dev | Requried to build programs that use FLTK + OpenGL
libfltk1.1-dev | Requried to build programs that use FLTK + OpenGL
libglu1-mesa-dev | Requried to build programs that use FLTK + OpenGL
libtiff4-dev | Requried to build programs that use FLTK + OpenGL
libxft | Requried to build programs that use FLTK + OpenGL
libxft-dev | Requried to build programs that use FLTK + OpenGL
fluid | To satisfy CMake’s FindFLTK module
ncurses-dev | Required to build MOOSRemote
python-dev | Required to build uVoice (not built by default)
swig | Required to build uVoice (not built by default)

### 1.4 Important CMake Variables

### 1.4.1 For FLTK

FLTK DIR - This is the library where CMake’s FindFLTK module expects to find the FLTK libraries. For mystifying reasons, it can’t figure out on its own to look in /usr/lib. You will probably want to set this to /usr/lib.

13

As a bonus, once you do so, MOOS’s customized version of that module, MOOSFindFLTK, will be able to figure out the proper value for FLTK_INCLUDE_DIR all by itself. As of this writing, IvP uses the standard version of FindFLTK which sadly cannot figure out the proper value for FLTK_INCLUDE_DIR after you’ve provided a valid value for FLTK_DIR.

FLTK INCLUDE DIR - The directory that is expected to include a subdirectory named FL, which in turn contains FLTK’s source files. On Ubuntu Linux 7.04, at least, the proper value for this is /usr/include.

### 1.4.2 For Python.h

IVP BUILD MOOS - When this is ON the build system will build uVoice, a Python wrapper for MOOS’s libraries. When this is ON you’ll need to set a proper value for the CMake variable PYTHON_INCLUDE_PATH or else the build processes won’t attempt to build uVoice.

PYTHON INCLUDE PATH - The directory containing the version of Python.h that should be used when building uVoice. On Ubuntu Linux 7.04, which
by default uses Python version 2.5, the correct value for this variable is /usr/include/python2.5, assuming that you’re trying to make a wrapper that works with the host system’s version of Python.

### 1.4.3 Other CMake Variables

IVP BUILD ... - There’s one of these variables for each program and library in the IvP part of the moos-ivp source tree. Setting a value to ON will cause the corresponding program or library to be included in the build process.
Several programs / libraries that were by default not built by the old build system have a default value of OFF for this variable. All others default to ON.

Note that the current IvP build system does not enforce, at this step, the build dependencies between libraries and the programs that require them at link-time. If you disable the building of a library but enable the building of some program that must be linked to that library, you’ll end up with an error from the linker when that program is being built.

BUILD ... - These come from the MOOS side of the project. Setting one of these variables to ON may lead to the appearance of even more such variables when you next configure the build tree, because MOOS’s build system supports a two-level hierarchy of dis-/en-abling the building of its programs and libraries.

14

CMAKE BUILD TYPE - By convention, any CMake variable whose name starts with CMAKE_ has special meaning to CMake. This variable controls details related to debug vs. optimized builds. Two noteworthy values are Debug and Release.

## 2 MOOS-IvP Build System Implementation Details

### 2.1 create-subdir-cmake-files.sh

IvP’s source tree contains about 79 libraries and applications as of this writing, each of which requires its own CMakeLists.txt file. Most IvP programs have similar needs for their CMakeLists.txt files, and the same goes for most IvP libraries.

Because this regularity exists, and because all 79 of those CMakeLists.txt files must be rewritten when certain improvements are made to the build system, IvP contains a script (plus a few helper files) to re-create those 79 CMakeLists.txt files whenever required.

That script is named create-subdir-cmake-files.sh. It and its support files are found in the directory

ivp/scripts/util/create-subdir-cmake-files/

Whenever a library or program is added to or removed from IvP, this script should be modified so that we can always easily recreate and / or redesign IvP’s build system.

As of this writing, this script only creates IvP’s CMakeLists.txt files, and none of MOOS’s. This is because the MOOS project already has a CMake-based build system in place and there’s no obvious need to re-implement it.

## 3 Future Work

### 3.1 Debian packaging

Debian packaging can be accomplished by some minor additions to IvP’s CMake-based build system. We’ve already submitted a patch for doing this in MOOS to Paul Newman, so the techniques and code have been worked out already.

15

### 3.2 RPM packaging

CMake 2.6, expected to be released in late 2007, should have a feature for easily producing RedHat Package Manager (RPM) software packages. When this happens we may support this for MOOS-IvP.

### 3.3 Windows builds

Now that all of MOOS-IvP can be built with CMake, we may be able to build the software on Windows with little or no additional effort.

[Note: Andrew Shafer has protested that this may be an overly optimistic assesment.]

### 3.4 Windows packaging

Develop an installation technique for MOOS-IvP that’s convenient for Windows programmers. We haven’t yet investigated what the most preferred form of packaging is.

### 3.5 Building Documentation

CMake can easily build man pages, Doxygen documentation, etc. Building it with CMake helps us to package the documentation for end-user use, as well as creating ...-doc Debian packages and whatever the RPM equivalent would be.

### 3.6 Building IvP’s Website

CMake’s scripting language should be sufficient for expressing how to create new versions of IvP’s static html website. This would be useful to ensure that the website is always synchronized with the most current release of our software and documentation.

16

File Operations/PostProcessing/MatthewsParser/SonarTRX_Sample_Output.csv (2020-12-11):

UTC+0.0 | Latitude | Longitude | Elevation | Heading | DepthBelowTransducer
2016-11-03T18:35:27.564 | 0 | 0 | 0 | 0 | 0
2016-11-03T18:35:28.655 | 0 | 0 | 0 | 0 | 0
2016-11-03T18:35:29.746 | 0 | 0 | 0 | 0 | 0
2016-11-03T18:35:30.837 | 0 | 0 | 0 | 0 | 0
2016-11-03T18:35:31.940 | 0 | 0 | 0 | 0 | 0
2016-11-03T18:35:33.000 | 0 | 0 | 0 | 0 | 0
2016-11-03T18:35:34.122 | 0 | 0 | 0 | 0 | 0
2016-11-03T18:35:35.213 | 0 | 0 | 0 | 0 | 0
2016-11-03T18:35:36.304 | 0 | 0 | 0 | 0 | 0
2016-11-03T18:35:37.420 | 0 | 0 | 0 | 0 | 0
2016-11-03T18:35:38.511 | 0 | 0 | 0 | 0 | 0
2016-11-03T18:35:39.602 | 0 | 0 | 0 | 0 | 0
2016-11-03T18:35:40.693 | 0 | 0 | 0 | 0 | 0
2016-11-03T18:35:41.784 | 0 | 0 | 0 | 0 | 0
2016-11-03T18:35:42.874 | 0 | 0 | 0 | 0 | 0
2016-11-03T18:35:43.965 | 0 | 0 | 0 | 0 | 0
2016-11-03T18:35:45.000 | 0 | 0 | 0 | 0 | 0
2016-11-03T18:35:46.147 | 0 | 0 | 0 | 0 | 0
2016-11-03T18:35:47.241 | 0 | 0 | 0 | 0 | 0
2016-11-03T18:35:48.332 | 0 | 0 | 0 | 0 | 0
2016-11-03T18:35:49.423 | 0 | 0 | 0 | 0 | 0
2016-11-03T18:35:50.514 | 0 | 0 | 0 | 0 | 0
2016-11-03T18:35:51.605 | 0 | 0 | 0 | 0 | 0
2016-11-03T18:35:52.700 | 0 | 0 | 0 | 0 | 0
2016-11-03T18:35:53.791 | 0 | 0 | 0 | 0 | 0
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

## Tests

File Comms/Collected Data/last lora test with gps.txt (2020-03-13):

Feather LoRa TX Test!
LoRa radio init OK!
Set Freq to: 915.00
Transmitting...
Sending Hello World #0
Sending...
Waiting for packet to complete...
Waiting for reply...
Got reply: And hello back to you
RSSI: -61
0 seconds is the longest break in contact so far.
Transmitting...
Sending Hello World #1
Sending...
Waiting for packet to complete...
Waiting for reply...
Got reply: And hello back to you
RSSI: -61
0 seconds is the longest break in contact so far.
Transmitting...
Sending Hello World #2
Sending...
Waiting for packet to complete...
Waiting for reply...
Got reply: And hello back to you
RSSI: -63
0 seconds is the longest break in contact so far.
Transmitting...
Sending Hello World #3
Sending...
Waiting for packet to complete...
Waiting for reply...
Got reply: And hello back to you
RSSI: -63
0 seconds is the longest break in contact so far.
Transmitting...
Sending Hello World #4
Sending...
Waiting for packet to complete...
Waiting for reply...
Got reply: And hello back to you
RSSI: -63
0 seconds is the longest break in contact so far.
Transmitting...
Sending Hello World #5
Sending...
Waiting for packet to complete...
Waiting for reply...
Got reply: And hello back to you
RSSI: -63
0 seconds is the longest break in contact so far.
Transmitting...
Sending Hello World #6
Sending...
Waiting for packet to complete...
Waiting for reply...
Got reply: And hello back to you
RSSI: -63
0 seconds is the longest break in contact so far.
Transmitting...
Sending Hello World #7
Sending...
Waiting for packet to complete...
Waiting for reply...
Got reply: And hello back to you
RSSI: -57
0 seconds is the longest break in contact so far.
Transmitting...
Sending Hello World #8
Sending...
Waiting for packet to complete...
Waiting for reply...
Got reply: And hello back to you
RSSI: -59
0 seconds is the longest break in contact so far.
Transmitting...
Sending Hello World #9
Sending...
Waiting for packet to complete...
Waiting for reply...
Got reply: And hello back to you
RSSI: -67
0 seconds is the longest break in contact so far.
Transmitting...
Sending Hello World #10
Sending...
Waiting for packet to complete...
Waiting for reply...
Got reply: And hello back to you
RSSI: -61
0 seconds is the longest break in contact so far.
Transmitting...
Sending Hello World #11
Sending...
Waiting for packet to complete...
Waiting for reply...
Got reply: And hello back to you
RSSI: -58
0 seconds is the longest break in contact so far.
Transmitting...
Sending Hello World #12
Sending...
Waiting for packet to complete...
Waiting for reply...
Got reply: And hello back to you
RSSI: -59
0 seconds is the longest break in contact so far.
Transmitting...
Sending Hello World #13
Sending...
Waiting for packet to complete...
Waiting for reply...
Got reply: And hello back to you
RSSI: -59
0 seconds is the longest break in contact so far.
Transmitting...
Sending Hello World #14
Sending...
Waiting for packet to complete...
Waiting for reply...
Got reply: And hello back to you
RSSI: -58
0 seconds is the longest break in contact so far.
Transmitting...
Sending Hello World #15
Sending...
Waiting for packet to complete...
Waiting for reply...
Got reply: And hello back to you
RSSI: -60
0 seconds is the longest break in contact so far.
Transmitting...
Sending Hello World #16
Sending...
Waiting for packet to complete...
Waiting for reply...
Got reply: And hello back to you
RSSI: -61
0 seconds is the longest break in contact so far.
Transmitting...
Sending Hello World #17
Sending...
Waiting for packet to complete...
Waiting for reply...
Got reply: And hello back to you
RSSI: -57
0 seconds is the longest break in contact so far.
Transmitting...
Sending Hello World #18
Sending...
Waiting for packet to complete...
Waiting for reply...
Got reply: And hello back to you
RSSI: -59
0 seconds is the longest break in contact so far.
Transmitting...
Sending Hello World #19
Sending...
Waiting for packet to complete...
Waiting for reply...
Got reply: And hello back to you
RSSI: -58
0 seconds is the longest break in contact so far.
Transmitting...
Sending Hello World #20
Sending...
Waiting for packet to complete...
Waiting for reply...
Got reply: And hello back to you
RSSI: -58
0 seconds is the longest break in contact so far.
Transmitting...
Sending Hello World #21
Sending...
Waiting for packet to complete...
Waiting for reply...
Got reply: And hello back to you
RSSI: -58
0 seconds is the longest break in contact so far.
Transmitting...
Sending Hello World #22
Sending...
Waiting for packet to complete...
Waiting for reply...
Got reply: And hello back to you
RSSI: -57
0 seconds is the longest break in contact so far.
Transmitting...
Sending Hello World #23
Sending...
Waiting for packet to complete...
Waiting for reply...
Got reply: And hello back to you
RSSI: -57
0 seconds is the longest break in contact so far.
Transmitting...
Sending Hello World #24
Sending...
Waiting for packet to complete...
Waiting for reply...
Got reply: And hello back to you
RSSI: -57
0 seconds is the longest break in contact so far.
Transmitting...
Sending Hello World #25
Sending...
Waiting for packet to complete...
Waiting for reply...
Got reply: And hello back to you
RSSI: -57
0 seconds is the longest break in contact so far.
Transmitting...
Sending Hello World #26
Sending...
Waiting for packet to complete...
Waiting for reply...
Got reply: And hello back to you
RSSI: -60
0 seconds is the longest break in contact so far.
Transmitting...
Sending Hello World #27
Sending...
Waiting for packet to complete...
Waiting for reply...
Got reply: And hello back to you
RSSI: -61
0 seconds is the longest break in contact so far.
Transmitting...
Sending Hello World #28
Sending...
Waiting for packet to complete...
Waiting for reply...
Got reply: And hello back to you
RSSI: -58
0 seconds is the longest break in contact so far.
Transmitting...
Sending Hello World #29
Sending...
Waiting for packet to complete...
Waiting for reply...
Got reply: And hello back to you
RSSI: -69
0 seconds is the longest break in contact so far.
Transmitting...
Sending Hello World #30
Sending...
Waiting for packet to complete...
Waiting for reply...
Got reply: And hello back to you
RSSI: -65
0 seconds is the longest break in contact so far.
Transmitting...
Sending Hello World #31
Sending...
Waiting for packet to complete...
Waiting for reply...
Got reply: And hello back to you
RSSI: -61
0 seconds is the longest break in contact so far.
Transmitting...
Sending Hello World #32
Sending...
Waiting for packet to complete...
Waiting for reply...
Got reply: And hello back to you
RSSI: -60
0 seconds is the longest break in contact so far.
Transmitting...
Sending Hello World #33
Sending...
Waiting for packet to complete...
Waiting for reply...
Got reply: And hello back to you
RSSI: -59
0 seconds is the longest break in contact so far.
Transmitting...
Sending Hello World #34
Sending...
Waiting for packet to complete...
Waiting for reply...
Got reply: And hello back to you
RSSI: -59
0 seconds is the longest break in contact so far.
Transmitting...
Sending Hello World #35
Sending...
Waiting for packet to complete...
Waiting for reply...
Got reply: And hello back to you
RSSI: -59
0 seconds is the longest break in contact so far.
Transmitting...
Sending Hello World #36
Sending...
Waiting for packet to complete...
Waiting for reply...
Got reply: And hello back to you
RSSI: -59
0 seconds is the longest break in contact so far.
Transmitting...
Sending Hello World #37
Sending...
Waiting for packet to complete...
Waiting for reply...
Got reply: And hello back to you
RSSI: -59
0 seconds is the longest break in contact so far.
Transmitting...
Sending Hello World #38
Sending...
Waiting for packet to complete...
Waiting for reply...
Got reply: And hello back to you
RSSI: -60
0 seconds is the longest break in contact so far.
Transmitting...
Sending Hello World #39
Sending...
Waiting for packet to complete...
Waiting for reply...
Got reply: And hello back to you
RSSI: -58
0 seconds is the longest break in contact so far.
Transmitting...
Sending Hello World #40
Sending...
Waiting for packet to complete...
Waiting for reply...
Got reply: And hello back to you
RSSI: -59
0 seconds is the longest break in contact so far.
Transmitting...
Sending Hello World #41
Sending...
Waiting for packet to complete...
Waiting for reply...
Got reply: And hello back to you
RSSI: -59
0 seconds is the longest break in contact so far.
Transmitting...
Sending Hello World #42
Sending...
Waiting for packet to complete...
Waiting for reply...
Got reply: And hello back to you
RSSI: -58
0 seconds is the longest break in contact so far.
Transmitting...
Sending Hello World #43
Sending...
Waiting for packet to complete...
Waiting for reply...
Got reply: And hello back to you
RSSI: -59
0 seconds is the longest break in contact so far.
Transmitting...
Sending Hello World #44
Sending...
Waiting for packet to complete...
Waiting for reply...
Got reply: And hello back to you
RSSI: -60
0 seconds is the longest break in contact so far.
Transmitting...
Sending Hello World #45
Sending...
Waiting for packet to complete...
Waiting for reply...
Got reply: And hello back to you
RSSI: -60
0 seconds is the longest break in contact so far.
Transmitting...
Sending Hello World #46
Sending...
Waiting for packet to complete...
Waiting for reply...
Got reply: And hello back to you
RSSI: -59
0 seconds is the longest break in contact so far.
Transmitting...
Sending Hello World #47
Sending...
Waiting for packet to complete...
Waiting for reply...
Got reply: And hello back to you
RSSI: -59
0 seconds is the longest break in contact so far.
Transmitting...
Sending Hello World #48
Sending...
Waiting for packet to complete...
Waiting for reply...
Got reply: And hello back to you
RSSI: -59
0 seconds is the longest break in contact so far.
Transmitting...
Sending Hello World #49
Sending...
Waiting for packet to complete...
Waiting for reply...
Got reply: And hello back to you
RSSI: -57
0 seconds is the longest break in contact so far.
Transmitting...
Sending Hello World #50
Sending...
Waiting for packet to complete...
Waiting for reply...
Got reply: And hello back to you
RSSI: -57
0 seconds is the longest break in contact so far.
Transmitting...
Sending Hello World #51
Sending...
Waiting for packet to complete...
Waiting for reply...
Got reply: And hello back to you
RSSI: -58
0 seconds is the longest break in contact so far.
Transmitting...
Sending Hello World #52
Sending...
Waiting for packet to complete...
Waiting for reply...
Got reply: And hello back to you
RSSI: -58
0 seconds is the longest break in contact so far.
Transmitting...
Sending Hello World #53
Sending...
Waiting for packet to complete...
Waiting for reply...
Got reply: And hello back to you
RSSI: -58
0 seconds is the longest break in contact so far.
Transmitting...
Sending Hello World #54
Sending...
Waiting for packet to complete...
Waiting for reply...
Got reply: And hello back to you
RSSI: -57
0 seconds is the longest break in contact so far.
Transmitting...
Sending Hello World #55
Sending...
Waiting for packet to complete...
Waiting for reply...
Got reply: And hello back to you
RSSI: -57
0 seconds is the longest break in contact so far.
Transmitting...
Sending Hello World #56
Sending...
Waiting for packet to complete...
Waiting for reply...
Got reply: And hello back to you
RSSI: -59
0 seconds is the longest break in contact so far.
Transmitting...
Sending Hello World #57
Sending...
Waiting for packet to complete...
Waiting for reply...
Got reply: And hello back to you
RSSI: -57
0 seconds is the longest break in contact so far.
Transmitting...
Sending Hello World #58
Sending...
Waiting for packet to complete...
Waiting for reply...
Got reply: And hello back to you
RSSI: -59
0 seconds is the longest break in contact so far.
Transmitting...
Sending Hello World #59
Sending...
Waiting for packet to complete...
Waiting for reply...
Got reply: And hello back to you
RSSI: -58
0 seconds is the longest break in contact so far.
Transmitting...
Sending Hello World #60
Sending...
Waiting for packet to complete...
Waiting for reply...
Got reply: And hello back to you
RSSI: -58
0 seconds is the longest break in contact so far.
Transmitting...
Sending Hello World #61
Sending...
Waiting for packet to complete...
Waiting for reply...
Got reply: And hello back to you
RSSI: -59
0 seconds is the longest break in contact so far.
Transmitting...
Sending Hello World #62
Sending...
Waiting for packet to complete...
Waiting for reply...
Got reply: And hello back to you
RSSI: -58
0 seconds is the longest break in contact so far.
Transmitting...
Sending Hello World #63
Sending...
Waiting for packet to complete...
Waiting for reply...
Got reply: And hello back to you
RSSI: -58
0 seconds is the longest break in contact so far.
Transmitting...
Sending Hello World #64
Sending...
Waiting for packet to complete...
Waiting for reply...
Got reply: And hello back to you
RSSI: -57
0 seconds is the longest break in contact so far.
Transmitting...
Sending Hello World #65
Sending...
Waiting for packet to complete...
Waiting for reply...
Got reply: And hello back to you
RSSI: -57
0 seconds is the longest break in contact so far.
Transmitting...
Sending Hello World #66
Sending...
Waiting for packet to complete...
Waiting for reply...
Got reply: And hello back to you
RSSI: -59
0 seconds is the longest break in contact so far.
Transmitting...
Sending Hello World #67
Sending...
Waiting for packet to complete...
Waiting for reply...
Got reply: And hello back to you
RSSI: -58
0 seconds is the longest break in contact so far.
Transmitting...
Sending Hello World #68
Sending...
Waiting for packet to complete...
Waiting for reply...
Got reply: And hello back to you
RSSI: -58
0 seconds is the longest break in contact so far.
Transmitting...
Sending Hello World #69
Sending...
Waiting for packet to complete...
Waiting for reply...
Got reply: And hello back to you
RSSI: -59
0 seconds is the longest break in contact so far.
Transmitting...
Sending Hello World #70
Sending...
Waiting for packet to complete...
Waiting for reply...
Got reply: And hello back to you
RSSI: -58
0 seconds is the longest break in contact so far.
Transmitting...
Sending Hello World #71
Sending...
Waiting for packet to complete...
Waiting for reply...
Got reply: And hello back to you
RSSI: -57
0 seconds is the longest break in contact so far.
Transmitting...
Sending Hello World #72
Sending...
Waiting for packet to complete...
Waiting for reply...
Got reply: And hello back to you
RSSI: -57
0 seconds is the longest break in contact so far.
Transmitting...
Sending Hello World #73
Sending...
Waiting for packet to complete...
Waiting for reply...
Got reply: And hello back to you
RSSI: -58
0 seconds is the longest break in contact so far.
Transmitting...
Sending Hello World #74
Sending...
Waiting for packet to complete...
Waiting for reply...
Got reply: And hello back to you
RSSI: -57
0 seconds is the longest break in contact so far.
Transmitting...
Sending Hello World #75
Sending...
Waiting for packet to complete...
Waiting for reply...
Got reply: And hello back to you
RSSI: -57
0 seconds is the longest break in contact so far.
Transmitting...
Sending Hello World #76
Sending...
Waiting for packet to complete...
Waiting for reply...
Got reply: And hello back to you
RSSI: -60
0 seconds is the longest break in contact so far.
Transmitting...
Sending Hello World #77
Sending...
Waiting for packet to complete...
Waiting for reply...
Got reply: And hello back to you
RSSI: -60
0 seconds is the longest break in contact so far.
Transmitting...
Sending Hello World #78
Sending...
Waiting for packet to complete...
Waiting for reply...
Got reply: And hello back to you
RSSI: -60
0 seconds is the longest break in contact so far.
Transmitting...
Sending Hello World #79
Sending...
Waiting for packet to complete...
Waiting for reply...
Got reply: And hello back to you
RSSI: -59
0 seconds is the longest break in contact so far.
Transmitting...
Sending Hello World #80
Sending...
Waiting for packet to complete...
Waiting for reply...
Got reply: And hello back to you
RSSI: -57
0 seconds is the longest break in contact so far.
Transmitting...
Sending Hello World #81
Sending...
Waiting for packet to complete...
Waiting for reply...
Got reply: And hello back to you
RSSI: -56
0 seconds is the longest break in contact so far.
Transmitting...
Sending Hello World #82
Sending...
Waiting for packet to complete...
Waiting for reply...
Got reply: And hello back to you
RSSI: -58
0 seconds is the longest break in contact so far.
Transmitting...
Sending Hello World #83
Sending...
Waiting for packet to complete...
Waiting for reply...
Got reply: And hello back to you
RSSI: -57
0 seconds is the longest break in contact so far.
Transmitting...
Sending Hello World #84
Sending...
Waiting for packet to complete...
Waiting for reply...
Got reply: And hello back to you
RSSI: -58
0 seconds is the longest break in contact so far.
Transmitting...
Sending Hello World #85
Sending...
Waiting for packet to complete...
Waiting for reply...
Got reply: And hello back to you
RSSI: -57
0 seconds is the longest break in contact so far.
Transmitting...
Sending Hello World #86
Sending...
Waiting for packet to complete...
Waiting for reply...
Got reply: And hello back to you
RSSI: -58
0 seconds is the longest break in contact so far.
Transmitting...
Sending Hello World #87
Sending...
Waiting for packet to complete...
Waiting for reply...
Got reply: And hello back to you
RSSI: -57
0 seconds is the longest break in contact so far.
Transmitting...
Sending Hello World #88
Sending...
Waiting for packet to complete...
Waiting for reply...
Got reply: And hello back to you
RSSI: -57
0 seconds is the longest break in contact so far.
Transmitting...
Sending Hello World #89
Sending...
Waiting for packet to complete...
Waiting for reply...
Got reply: And hello back to you
RSSI: -57
0 seconds is the longest break in contact so far.
Transmitting...
Sending Hello World #90
Sending...
Waiting for packet to complete...
Waiting for reply...
Got reply: And hello back to you
RSSI: -57
0 seconds is the longest break in contact so far.
Transmitting...
Sending Hello World #91
Sending...
Waiting for packet to complete...
Waiting for reply...
Got reply: And hello back to you
RSSI: -57
0 seconds is the longest break in contact so far.
Transmitting...
Sending Hello World #92
Sending...
Waiting for packet to complete...
Waiting for reply...
Got reply: And hello back to you
RSSI: -58
0 seconds is the longest break in contact so far.
Transmitting...
Sending Hello World #93
Sending...
Waiting for packet to complete...
Waiting for reply...
Got reply: And hello back to you
RSSI: -57
0 seconds is the longest break in contact so far.
Transmitting...
Sending Hello World #94
Sending...
Waiting for packet to complete...
Waiting for reply...
Got reply: And hello back to you
RSSI: -58
0 seconds is the longest break in contact so far.
Transmitting...
Sending Hello World #95
Sending...
Waiting for packet to complete...
Waiting for reply...
Got reply: And hello back to you
RSSI: -61
0 seconds is the longest break in contact so far.
Transmitting...
Sending Hello World #96
Sending...
Waiting for packet to complete...
Waiting for reply...
Got reply: And hello back to you
RSSI: -58
0 seconds is the longest break in contact so far.
Transmitting...
Sending Hello World #97
Sending...
Waiting for packet to complete...
Waiting for reply...
Got reply: And hello back to you
RSSI: -57
0 seconds is the longest break in contact so far.
Transmitting...
Sending Hello World #98
Sending...
Waiting for packet to complete...
Waiting for reply...
Got reply: And hello back to you
RSSI: -58
0 seconds is the longest break in contact so far.
Transmitting...
Sending Hello World #99
Sending...
Waiting for packet to complete...
Waiting for reply...
Got reply: And hello back to you
RSSI: -63
0 seconds is the longest break in contact so far.
Transmitting...
Sending Hello World #100
Sending...
Waiting for packet to complete...
Waiting for reply...
Got reply: And hello back to you
RSSI: -60
0 seconds is the longest break in contact so far.
Transmitting...
Sending Hello World #101
Sending...
Waiting for packet to complete...
Waiting for reply...
Got reply: And hello back to you
RSSI: -58
0 seconds is the longest break in contact so far.
Transmitting...
Sending Hello World #102
Sending...
Waiting for packet to complete...
Waiting for reply...
Got reply: And hello back to you
RSSI: -60
0 seconds is the longest break in contact so far.
Transmitting...
Sending Hello World #103
Sending...
Waiting for packet to complete...
Waiting for reply...
Got reply: And hello back to you
RSSI: -59
0 seconds is the longest break in contact so far.
Transmitting...
Sending Hello World #104
Sending...
Waiting for packet to complete...
Waiting for reply...
Got reply: And hello back to you
RSSI: -58
0 seconds is the longest break in contact so far.
Transmitting...
Sending Hello World #105
Sending...
Waiting for packet to complete...
Waiting for reply...
Got reply: And hello back to you
RSSI: -58
0 seconds is the longest break in contact so far.
Transmitting...
Sending Hello World #106
Sending...
Waiting for packet to complete...
Waiting for reply...
Got reply: And hello back to you
RSSI: -59
0 seconds is the longest break in contact so far.
Transmitting...
Sending Hello World #107
Sending...
Waiting for packet to complete...
Waiting for reply...
Got reply: And hello back to you
RSSI: -58
0 seconds is the longest break in contact so far.
Transmitting...
Sending Hello World #108
Sending...
Waiting for packet to complete...
Waiting for reply...
Got reply: And hello back to you
RSSI: -59
0 seconds is the longest break in contact so far.
Transmitting...
Sending Hello World #109
Sending...
Waiting for packet to complete...
Waiting for reply...
Got reply: And hello back to you
RSSI: -68
0 seconds is the longest break in contact so far.
Transmitting...
Sending Hello World #110
Sending...
Waiting for packet to complete...
Waiting for reply...
Got reply: And hello back to you
RSSI: -58
0 seconds is the longest break in contact so far.
Transmitting...
Sending Hello World #111
Sending...
Waiting for packet to complete...
Waiting for reply...
Got reply: And hello back to you
RSSI: -58
0 seconds is the longest break in contact so far.
Transmitting...
Sending Hello World #112
Sending...
Waiting for packet to complete...
Waiting for reply...
Got reply: And hello back to you
RSSI: -58
0 seconds is the longest break in contact so far.
Transmitting...
Sending Hello World #113
Sending...
Waiting for packet to complete...
Waiting for reply...
Got reply: And hello back to you
RSSI: -59
0 seconds is the longest break in contact so far.
Transmitting...
Sending Hello World #114
Sending...
Waiting for packet to complete...
Waiting for reply...
Got reply: And hello back to you
RSSI: -58
0 seconds is the longest break in contact so far.
Transmitting...
Sending Hello World #115
Sending...
Waiting for packet to complete...
Waiting for reply...
Got reply: And hello back to you
RSSI: -57
0 seconds is the longest break in contact so far.
Transmitting...
Sending Hello World #116
Sending...
Waiting for packet to complete...
Waiting for reply...
Got reply: And hello back to you
RSSI: -54
0 seconds is the longest break in contact so far.
Transmitting...
Sending Hello World #117
Sending...
Waiting for packet to complete...
Waiting for reply...
Got reply: And hello back to you
RSSI: -58
0 seconds is the longest break in contact so far.
Transmitting...
Sending Hello World #118
Sending...
Waiting for packet to complete...
Waiting for reply...
Got reply: And hello back to you
RSSI: -65
0 seconds is the longest break in contact so far.
Transmitting...
Sending Hello World #119
Sending...
Waiting for packet to complete...
Waiting for reply...
Got reply: And hello back to you
RSSI: -64
0 seconds is the longest break in contact so far.
Transmitting...
Sending Hello World #120
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

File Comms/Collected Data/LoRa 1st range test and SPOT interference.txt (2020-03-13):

Sending Hello World #778
Sending...
Waiting for packet to complete...
Waiting for reply...
Got reply: And hello back to you
RSSI: -54
2 seconds is the longest break in contact so far.
Transmitting...
Sending Hello World #779
Sending...
Waiting for packet to complete...
Waiting for reply...
Got reply: And hello back to you
RSSI: -53
2 seconds is the longest break in contact so far.
Transmitting...
Sending Hello World #780
Sending...
Waiting for packet to complete...
Waiting for reply...
Got reply: And hello back to you
RSSI: -55
2 seconds is the longest break in contact so far.
Transmitting...
Sending Hello World #781
Sending...
Waiting for packet to complete...
Waiting for reply...
Got reply: And hello back to you
RSSI: -54
2 seconds is the longest break in contact so far.
Transmitting...
Sending Hello World #782
Sending...
Waiting for packet to complete...
Waiting for reply...
Got reply: And hello back to you
RSSI: -54
2 seconds is the longest break in contact so far.
Transmitting...
Sending Hello World #783
Sending...
Waiting for packet to complete...
Waiting for reply...
Got reply: And hello back to you
RSSI: -54
2 seconds is the longest break in contact so far.
Transmitting...
Sending Hello World #784
Sending...
Waiting for packet to complete...
Waiting for reply...
Got reply: And hello back to you
RSSI: -54
2 seconds is the longest break in contact so far.
Transmitting...
Sending Hello World #785
Sending...
Waiting for packet to complete...
Waiting for reply...
Got reply: And hello back to you
RSSI: -54
2 seconds is the longest break in contact so far.
Transmitting...
Sending Hello World #786
Sending...
Waiting for packet to complete...
Waiting for reply...
Got reply: And hello back to you
RSSI: -54
2 seconds is the longest break in contact so far.
Transmitting...
Sending Hello World #787
Sending...
Waiting for packet to complete...
Waiting for reply...
Got reply: And hello back to you
RSSI: -53
2 seconds is the longest break in contact so far.
Transmitting...
Sending Hello World #788
Sending...
Waiting for packet to complete...
Waiting for reply...
Got reply: And hello back to you
RSSI: -53
2 seconds is the longest break in contact so far.
Transmitting...
Sending Hello World #789
Sending...
Waiting for packet to complete...
Waiting for reply...
Got reply: And hello back to you
RSSI: -54
2 seconds is the longest break in contact so far.
Transmitting...
Sending Hello World #790
Sending...
Waiting for packet to complete...
Waiting for reply...
Got reply: And hello back to you
RSSI: -53
2 seconds is the longest break in contact so far.
Transmitting...
Sending Hello World #791
Sending...
Waiting for packet to complete...
Waiting for reply...
Got reply: And hello back to you
RSSI: -53
2 seconds is the longest break in contact so far.
Transmitting...
Sending Hello World #792
Sending...
Waiting for packet to complete...
Waiting for reply...
Got reply: And hello back to you
RSSI: -53
2 seconds is the longest break in contact so far.
Transmitting...
Sending Hello World #793
Sending...
Waiting for packet to complete...
Waiting for reply...
Got reply: And hello back to you
RSSI: -53
2 seconds is the longest break in contact so far.
Transmitting...
Sending Hello World #794
Sending...
Waiting for packet to complete...
Waiting for reply...
Got reply: And hello back to you
RSSI: -53
2 seconds is the longest break in contact so far.
Transmitting...
Sending Hello World #795
Sending...
Waiting for packet to complete...
Waiting for reply...
Got reply: And hello back to you
RSSI: -54
2 seconds is the longest break in contact so far.
Transmitting...
Sending Hello World #796
Sending...
Waiting for packet to complete...
Waiting for reply...
Got reply: And hello back to you
RSSI: -57
2 seconds is the longest break in contact so far.
Transmitting...
Sending Hello World #797
Sending...
Waiting for packet to complete...
Waiting for reply...
Got reply: And hello back to you
RSSI: -56
2 seconds is the longest break in contact so far.
Transmitting...
Sending Hello World #798
Sending...
Waiting for packet to complete...
Waiting for reply...
Got reply: And hello back to you
RSSI: -59
2 seconds is the longest break in contact so far.
Transmitting...
Sending Hello World #799
Sending...
Waiting for packet to complete...
Waiting for reply...
Got reply: And hello back to you
RSSI: -56
2 seconds is the longest break in contact so far.
Transmitting...
Sending Hello World #800
Sending...
Waiting for packet to complete...
Waiting for reply...
Got reply: And hello back to you
RSSI: -51
2 seconds is the longest break in contact so far.
Transmitting...
Sending Hello World #801
Sending...
Waiting for packet to complete...
Waiting for reply...
Got reply: And hello back to you
RSSI: -55
2 seconds is the longest break in contact so far.
Transmitting...
Sending Hello World #802
Sending...
Waiting for packet to complete...
Waiting for reply...
Got reply: And hello back to you
RSSI: -59
2 seconds is the longest break in contact so far.
Transmitting...
Sending Hello World #803
Sending...
Waiting for packet to complete...
Waiting for reply...
Got reply: And hello back to you
RSSI: -58
2 seconds is the longest break in contact so far.
Transmitting...
Sending Hello World #804
Sending...
Waiting for packet to complete...
Waiting for reply...
Got reply: And hello back to you
RSSI: -65
2 seconds is the longest break in contact so far.
Transmitting...
Sending Hello World #805
Sending...
Waiting for packet to complete...
Waiting for reply...
Got reply: And hello back to you
RSSI: -66
2 seconds is the longest break in contact so far.
Transmitting...
Sending Hello World #806
Sending...
Waiting for packet to complete...
Waiting for reply...
Got reply: And hello back to you
RSSI: -67
2 seconds is the longest break in contact so far.
Transmitting...
Sending Hello World #807
Sending...
Waiting for packet to complete...
Waiting for reply...
Got reply: And hello back to you
RSSI: -72
2 seconds is the longest break in contact so far.
Transmitting...
Sending Hello World #808
Sending...
Waiting for packet to complete...
Waiting for reply...
Got reply: And hello back to you
RSSI: -64
2 seconds is the longest break in contact so far.
Transmitting...
Sending Hello World #809
Sending...
Waiting for packet to complete...
Waiting for reply...
Got reply: And hello back to you
RSSI: -67
2 seconds is the longest break in contact so far.
Transmitting...
Sending Hello World #810
Sending...
Waiting for packet to complete...
Waiting for reply...
Got reply: And hello back to you
RSSI: -67
2 seconds is the longest break in contact so far.
Transmitting...
Sending Hello World #811
Sending...
Waiting for packet to complete...
Waiting for reply...
Got reply: And hello back to you
RSSI: -65
2 seconds is the longest break in contact so far.
Transmitting...
Sending Hello World #812
Sending...
Waiting for packet to complete...
Waiting for reply...
Got reply: And hello back to you
RSSI: -70
2 seconds is the longest break in contact so far.
Transmitting...
Sending Hello World #813
Sending...
Waiting for packet to complete...
Waiting for reply...
Got reply: And hello back to you
RSSI: -82
2 seconds is the longest break in contact so far.
Transmitting...
Sending Hello World #814
Sending...
Waiting for packet to complete...
Waiting for reply...
Got reply: And hello back to you
RSSI: -80
2 seconds is the longest break in contact so far.
Transmitting...
Sending Hello World #815
Sending...
Waiting for packet to complete...
Waiting for reply...
Got reply: And hello back to you
RSSI: -83
2 seconds is the longest break in contact so far.
Transmitting...
Sending Hello World #816
Sending...
Waiting for packet to complete...
Waiting for reply...
Got reply: And hello back to you
RSSI: -83
2 seconds is the longest break in contact so far.
Transmitting...
Sending Hello World #817
Sending...
Waiting for packet to complete...
Waiting for reply...
Got reply: And hello back to you
RSSI: -69
2 seconds is the longest break in contact so far.
Transmitting...
Sending Hello World #818
Sending...
Waiting for packet to complete...
Waiting for reply...
Got reply: And hello back to you
RSSI: -73
2 seconds is the longest break in contact so far.
Transmitting...
Sending Hello World #819
Sending...
Waiting for packet to complete...
Waiting for reply...
Got reply: And hello back to you
RSSI: -72
2 seconds is the longest break in contact so far.
Transmitting...
Sending Hello World #820
Sending...
Waiting for packet to complete...
Waiting for reply...
Got reply: And hello back to you
RSSI: -80
2 seconds is the longest break in contact so far.
Transmitting...
Sending Hello World #821
Sending...
Waiting for packet to complete...
Waiting for reply...
Got reply: And hello back to you
RSSI: -72
2 seconds is the longest break in contact so far.
Transmitting...
Sending Hello World #822
Sending...
Waiting for packet to complete...
Waiting for reply...
Got reply: And hello back to you
RSSI: -66
2 seconds is the longest break in contact so far.
Transmitting...
Sending Hello World #823
Sending...
Waiting for packet to complete...
Waiting for reply...
Got reply: And hello back to you
RSSI: -73
2 seconds is the longest break in contact so far.
Transmitting...
Sending Hello World #824
Sending...
Waiting for packet to complete...
Waiting for reply...
Got reply: And hello back to you
RSSI: -71
2 seconds is the longest break in contact so far.
Transmitting...
Sending Hello World #825
Sending...
Waiting for packet to complete...
Waiting for reply...
Got reply: And hello back to you
RSSI: -67
2 seconds is the longest break in contact so far.
Transmitting...
Sending Hello World #826
Sending...
Waiting for packet to complete...
Waiting for reply...
Got reply: And hello back to you
RSSI: -69
2 seconds is the longest break in contact so far.
Transmitting...
Sending Hello World #827
Sending...
Waiting for packet to complete...
Waiting for reply...
Got reply: And hello back to you
RSSI: -68
2 seconds is the longest break in contact so far.
Transmitting...
Sending Hello World #828
Sending...
Waiting for packet to complete...
Waiting for reply...
Got reply: And hello back to you
RSSI: -70
2 seconds is the longest break in contact so far.
Transmitting...
Sending Hello World #829
Sending...
Waiting for packet to complete...
Waiting for reply...
Got reply: And hello back to you
RSSI: -68
2 seconds is the longest break in contact so far.
Transmitting...
Sending Hello World #830
Sending...
Waiting for packet to complete...
Waiting for reply...
Got reply: And hello back to you
RSSI: -74
2 seconds is the longest break in contact so far.
Transmitting...
Sending Hello World #831
Sending...
Waiting for packet to complete...
Waiting for reply...
Got reply: And hello back to you
RSSI: -72
2 seconds is the longest break in contact so far.
Transmitting...
Sending Hello World #832
Sending...
Waiting for packet to complete...
Waiting for reply...
Got reply: And hello back to you
RSSI: -67
2 seconds is the longest break in contact so far.
Transmitting...
Sending Hello World #833
Sending...
Waiting for packet to complete...
Waiting for reply...
Got reply: And hello back to you
RSSI: -72
2 seconds is the longest break in contact so far.
Transmitting...
Sending Hello World #834
Sending...
Waiting for packet to complete...
Waiting for reply...
Got reply: And hello back to you
RSSI: -77
2 seconds is the longest break in contact so far.
Transmitting...
Sending Hello World #835
Sending...
Waiting for packet to complete...
Waiting for reply...
Got reply: And hello back to you
RSSI: -74
2 seconds is the longest break in contact so far.
Transmitting...
Sending Hello World #836
Sending...
Waiting for packet to complete...
Waiting for reply...
Got reply: And hello back to you
RSSI: -76
2 seconds is the longest break in contact so far.
Transmitting...
Sending Hello World #837
Sending...
Waiting for packet to complete...
Waiting for reply...
Got reply: And hello back to you
RSSI: -87
2 seconds is the longest break in contact so far.
Transmitting...
Sending Hello World #838
Sending...
Waiting for packet to complete...
Waiting for reply...
Got reply: And hello back to you
RSSI: -81
2 seconds is the longest break in contact so far.
Transmitting...
Sending Hello World #839
Sending...
Waiting for packet to complete...
Waiting for reply...
Got reply: And hello back to you
RSSI: -81
2 seconds is the longest break in contact so far.
Transmitting...
Sending Hello World #840
Sending...
Waiting for packet to complete...
Waiting for reply...
Got reply: And hello back to you
RSSI: -92
2 seconds is the longest break in contact so far.
Transmitting...
Sending Hello World #841
Sending...
Waiting for packet to complete...
Waiting for reply...
Got reply: And hello back to you
RSSI: -83
2 seconds is the longest break in contact so far.
Transmitting...
Sending Hello World #842
Sending...
Waiting for packet to complete...
Waiting for reply...
Got reply: And hello back to you
RSSI: -83
2 seconds is the longest break in contact so far.
Transmitting...
Sending Hello World #843
Sending...
Waiting for packet to complete...
Waiting for reply...
Got reply: And hello back to you
RSSI: -79
2 seconds is the longest break in contact so far.
Transmitting...
Sending Hello World #844
Sending...
Waiting for packet to complete...
Waiting for reply...
Got reply: And hello back to you
RSSI: -83
2 seconds is the longest break in contact so far.
Transmitting...
Sending Hello World #845
Sending...
Waiting for packet to complete...
Waiting for reply...
Got reply: And hello back to you
RSSI: -96
2 seconds is the longest break in contact so far.
Transmitting...
Sending Hello World #846
Sending...
Waiting for packet to complete...
Waiting for reply...
Got reply: And hello back to you
RSSI: -74
2 seconds is the longest break in contact so far.
Transmitting...
Sending Hello World #847
Sending...
Waiting for packet to complete...
Waiting for reply...
No reply, is there a listener around?
Receive failed. 2 seconds since last contact.
2 seconds is the longest break in contact so far.
Transmitting...
Sending Hello World #848
Sending...
Waiting for packet to complete...
Waiting for reply...
Got reply: And hello back to you
RSSI: -85
2 seconds is the longest break in contact so far.
Transmitting...
Sending Hello World #849
Sending...
Waiting for packet to complete...
Waiting for reply...
Got reply: And hello back to you
RSSI: -75
2 seconds is the longest break in contact so far.
Transmitting...
Sending Hello World #850
Sending...
Waiting for packet to complete...
Waiting for reply...
Got reply: And hello back to you
RSSI: -88
2 seconds is the longest break in contact so far.
Transmitting...
Sending Hello World #851
Sending...
Waiting for packet to complete...
Waiting for reply...
Got reply: And hello back to you
RSSI: -88
2 seconds is the longest break in contact so far.
Transmitting...
Sending Hello World #852
Sending...
Waiting for packet to complete...
Waiting for reply...
Got reply: And hello back to you
RSSI: -86
2 seconds is the longest break in contact so far.
Transmitting...
Sending Hello World #853
Sending...
Waiting for packet to complete...
Waiting for reply...
Got reply: And hello back to you
RSSI: -81
2 seconds is the longest break in contact so far.
Transmitting...
Sending Hello World #854
Sending...
Waiting for packet to complete...
Waiting for reply...
Got reply: And hello back to you
RSSI: -86
2 seconds is the longest break in contact so far.
Transmitting...
Sending Hello World #855
Sending...
Waiting for packet to complete...
Waiting for reply...
Got reply: And hello back to you
RSSI: -79
2 seconds is the longest break in contact so far.
Transmitting...
Sending Hello World #856
Sending...
Waiting for packet to complete...
Waiting for reply...
Got reply: And hello back to you
RSSI: -73
2 seconds is the longest break in contact so far.
Transmitting...
Sending Hello World #857
Sending...
Waiting for packet to complete...
Waiting for reply...
No reply, is there a listener around?
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

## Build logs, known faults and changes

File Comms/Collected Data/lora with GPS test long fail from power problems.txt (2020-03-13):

Sending Hello World #551
Sending...
Waiting for packet to complete...
Waiting for reply...
Got reply: And hello back to you
RSSI: -64
2 seconds is the longest break in contact so far.
Transmitting...
Sending Hello World #552
Sending...
Waiting for packet to complete...
Waiting for reply...
Got reply: And hello back to you
RSSI: -61
2 seconds is the longest break in contact so far.
Transmitting...
Sending Hello World #553
Sending...
Waiting for packet to complete...
Waiting for reply...
Got reply: And hello back to you
RSSI: -61
2 seconds is the longest break in contact so far.
Transmitting...
Sending Hello World #554
Sending...
Waiting for packet to complete...
Waiting for reply...
Got reply: And hello back to you
RSSI: -60
2 seconds is the longest break in contact so far.
Transmitting...
Sending Hello World #555
Sending...
Waiting for packet to complete...
Waiting for reply...
Got reply: And hello back to you
RSSI: -60
2 seconds is the longest break in contact so far.
Transmitting...
Sending Hello World #556
Sending...
Waiting for packet to complete...
Waiting for reply...
Got reply: And hello back to you
RSSI: -61
2 seconds is the longest break in contact so far.
Transmitting...
Sending Hello World #557
Sending...
Waiting for packet to complete...
Waiting for reply...
Got reply: And hello back to you
RSSI: -60
2 seconds is the longest break in contact so far.
Transmitting...
Sending Hello World #558
Sending...
Waiting for packet to complete...
Waiting for reply...
Got reply: And hello back to you
RSSI: -61
2 seconds is the longest break in contact so far.
Transmitting...
Sending Hello World #559
Sending...
Waiting for packet to complete...
Waiting for reply...
Got reply: And hello back to you
RSSI: -63
2 seconds is the longest break in contact so far.
Transmitting...
Sending Hello World #560
Sending...
Waiting for packet to complete...
Waiting for reply...
Got reply: And hello back to you
RSSI: -63
2 seconds is the longest break in contact so far.
Transmitting...
Sending Hello World #561
Sending...
Waiting for packet to complete...
Waiting for reply...
Got reply: And hello back to you
RSSI: -61
2 seconds is the longest break in contact so far.
Transmitting...
Sending Hello World #562
Sending...
Waiting for packet to complete...
Waiting for reply...
Got reply: And hello back to you
RSSI: -61
2 seconds is the longest break in contact so far.
Transmitting...
Sending Hello World #563
Sending...
Waiting for packet to complete...
Waiting for reply...
Got reply: And hello back to you
RSSI: -61
2 seconds is the longest break in contact so far.
Transmitting...
Sending Hello World #564
Sending...
Waiting for packet to complete...
Waiting for reply...
Got reply: And hello back to you
RSSI: -60
2 seconds is the longest break in contact so far.
Transmitting...
Sending Hello World #565
Sending...
Waiting for packet to complete...
Waiting for reply...
Got reply: And hello back to you
RSSI: -61
2 seconds is the longest break in contact so far.
Transmitting...
Sending Hello World #566
Sending...
Waiting for packet to complete...
Waiting for reply...
Got reply: And hello back to you
RSSI: -63
2 seconds is the longest break in contact so far.
Transmitting...
Sending Hello World #567
Sending...
Waiting for packet to complete...
Waiting for reply...
Got reply: And hello back to you
RSSI: -64
2 seconds is the longest break in contact so far.
Transmitting...
Sending Hello World #568
Sending...
Waiting for packet to complete...
Waiting for reply...
Got reply: And hello back to you
RSSI: -64
2 seconds is the longest break in contact so far.
Transmitting...
Sending Hello World #569
Sending...
Waiting for packet to complete...
Waiting for reply...
Got reply: And hello back to you
RSSI: -63
2 seconds is the longest break in contact so far.
Transmitting...
Sending Hello World #570
Sending...
Waiting for packet to complete...
Waiting for reply...
Got reply: And hello back to you
RSSI: -61
2 seconds is the longest break in contact so far.
Transmitting...
Sending Hello World #571
Sending...
Waiting for packet to complete...
Waiting for reply...
Got reply: And hello back to you
RSSI: -63
2 seconds is the longest break in contact so far.
Transmitting...
Sending Hello World #572
Sending...
Waiting for packet to complete...
Waiting for reply...
Got reply: And hello back to you
RSSI: -64
2 seconds is the longest break in contact so far.
Transmitting...
Sending Hello World #573
Sending...
Waiting for packet to complete...
Waiting for reply...
Got reply: And hello back to you
RSSI: -67
2 seconds is the longest break in contact so far.
Transmitting...
Sending Hello World #574
Sending...
Waiting for packet to complete...
Waiting for reply...
Got reply: And hello back to you
RSSI: -61
2 seconds is the longest break in contact so far.
Transmitting...
Sending Hello World #575
Sending...
Waiting for packet to complete...
Waiting for reply...
Got reply: And hello back to you
RSSI: -63
2 seconds is the longest break in contact so far.
Transmitting...
Sending Hello World #576
Sending...
Waiting for packet to complete...
Waiting for reply...
Got reply: And hello back to you
RSSI: -61
2 seconds is the longest break in contact so far.
Transmitting...
Sending Hello World #577
Sending...
Waiting for packet to complete...
Waiting for reply...
Got reply: And hello back to you
RSSI: -60
2 seconds is the longest break in contact so far.
Transmitting...
Sending Hello World #578
Sending...
Waiting for packet to complete...
Waiting for reply...
Got reply: And hello back to you
RSSI: -64
2 seconds is the longest break in contact so far.
Transmitting...
Sending Hello World #579
Sending...
Waiting for packet to complete...
Waiting for reply...
Got reply: And hello back to you
RSSI: -64
2 seconds is the longest break in contact so far.
Transmitting...
Sending Hello World #580
Sending...
Waiting for packet to complete...
Waiting for reply...
Got reply: And hello back to you
RSSI: -61
2 seconds is the longest break in contact so far.
Transmitting...
Sending Hello World #581
Sending...
Waiting for packet to complete...
Waiting for reply...
Got reply: And hello back to you
RSSI: -60
2 seconds is the longest break in contact so far.
Transmitting...
Sending Hello World #582
Sending...
Waiting for packet to complete...
Waiting for reply...
Got reply: And hello back to you
RSSI: -60
2 seconds is the longest break in contact so far.
Transmitting...
Sending Hello World #583
Sending...
Waiting for packet to complete...
Waiting for reply...
Got reply: And hello back to you
RSSI: -61
2 seconds is the longest break in contact so far.
Transmitting...
Sending Hello World #584
Sending...
Waiting for packet to complete...
Waiting for reply...
Got reply: And hello back to you
RSSI: -61
2 seconds is the longest break in contact so far.
Transmitting...
Sending Hello World #585
Sending...
Waiting for packet to complete...
Waiting for reply...
Got reply: And hello back to you
RSSI: -63
2 seconds is the longest break in contact so far.
Transmitting...
Sending Hello World #586
Sending...
Waiting for packet to complete...
Waiting for reply...
Got reply: And hello back to you
RSSI: -60
2 seconds is the longest break in contact so far.
Transmitting...
Sending Hello World #587
Sending...
Waiting for packet to complete...
Waiting for reply...
Got reply: And hello back to you
RSSI: -61
2 seconds is the longest break in contact so far.
Transmitting...
Sending Hello World #588
Sending...
Waiting for packet to complete...
Waiting for reply...
Got reply: And hello back to you
RSSI: -60
2 seconds is the longest break in contact so far.
Transmitting...
Sending Hello World #589
Sending...
Waiting for packet to complete...
Waiting for reply...
Got reply: And hello back to you
RSSI: -61
2 seconds is the longest break in contact so far.
Transmitting...
Sending Hello World #590
Sending...
Waiting for packet to complete...
Waiting for reply...
Got reply: And hello back to you
RSSI: -60
2 seconds is the longest break in contact so far.
Transmitting...
Sending Hello World #591
Sending...
Waiting for packet to complete...
Waiting for reply...
Got reply: And hello back to you
RSSI: -59
2 seconds is the longest break in contact so far.
Transmitting...
Sending Hello World #592
Sending...
Waiting for packet to complete...
Waiting for reply...
Got reply: And hello back to you
RSSI: -61
2 seconds is the longest break in contact so far.
Transmitting...
Sending Hello World #593
Sending...
Waiting for packet to complete...
Waiting for reply...
Got reply: And hello back to you
RSSI: -59
2 seconds is the longest break in contact so far.
Transmitting...
Sending Hello World #594
Sending...
Waiting for packet to complete...
Waiting for reply...
Got reply: And hello back to you
RSSI: -70
2 seconds is the longest break in contact so far.
Transmitting...
Sending Hello World #595
Sending...
Waiting for packet to complete...
Waiting for reply...
No reply, is there a listener around?
Receive failed. 2 seconds since last contact.
2 seconds is the longest break in contact so far.
Transmitting...
Sending Hello World #596
Sending...
Waiting for packet to complete...
Waiting for reply...
No reply, is there a listener around?
Receive failed. 4 seconds since last contact.
4 seconds is the longest break in contact so far.
Transmitting...
Sending Hello World #597
Sending...
Waiting for packet to complete...
Waiting for reply...
No reply, is there a listener around?
Receive failed. 6 seconds since last contact.
6 seconds is the longest break in contact so far.
Transmitting...
Sending Hello World #598
Sending...
Waiting for packet to complete...
Waiting for reply...
No reply, is there a listener around?
Receive failed. 8 seconds since last contact.
8 seconds is the longest break in contact so far.
Transmitting...
Sending Hello World #599
Sending...
Waiting for packet to complete...
Waiting for reply...
No reply, is there a listener around?
Receive failed. 10 seconds since last contact.
10 seconds is the longest break in contact so far.
Transmitting...
Sending Hello World #600
Sending...
Waiting for packet to complete...
Waiting for reply...
No reply, is there a listener around?
Receive failed. 12 seconds since last contact.
12 seconds is the longest break in contact so far.
Transmitting...
Sending Hello World #601
Sending...
Waiting for packet to complete...
Waiting for reply...
No reply, is there a listener around?
Receive failed. 14 seconds since last contact.
14 seconds is the longest break in contact so far.
Transmitting...
Sending Hello World #602
Sending...
Waiting for packet to complete...
Waiting for reply...
No reply, is there a listener around?
Receive failed. 16 seconds since last contact.
16 seconds is the longest break in contact so far.
Transmitting...
Sending Hello World #603
Sending...
Waiting for packet to complete...
Waiting for reply...
No reply, is there a listener around?
Receive failed. 18 seconds since last contact.
18 seconds is the longest break in contact so far.
Transmitting...
Sending Hello World #604
Sending...
Waiting for packet to complete...
Waiting for reply...
No reply, is there a listener around?
Receive failed. 20 seconds since last contact.
20 seconds is the longest break in contact so far.
Transmitting...
Sending Hello World #605
Sending...
Waiting for packet to complete...
Waiting for reply...
No reply, is there a listener around?
Receive failed. 22 seconds since last contact.
22 seconds is the longest break in contact so far.
Transmitting...
Sending Hello World #606
Sending...
Waiting for packet to complete...
Waiting for reply...
No reply, is there a listener around?
Receive failed. 24 seconds since last contact.
24 seconds is the longest break in contact so far.
Transmitting...
Sending Hello World #607
Sending...
Waiting for packet to complete...
Waiting for reply...
No reply, is there a listener around?
Receive failed. 26 seconds since last contact.
26 seconds is the longest break in contact so far.
Transmitting...
Sending Hello World #608
Sending...
Waiting for packet to complete...
Waiting for reply...
No reply, is there a listener around?
Receive failed. 29 seconds since last contact.
29 seconds is the longest break in contact so far.
Transmitting...
Sending Hello World #609
Sending...
Waiting for packet to complete...
Waiting for reply...
No reply, is there a listener around?
Receive failed. 31 seconds since last contact.
31 seconds is the longest break in contact so far.
Transmitting...
Sending Hello World #610
Sending...
Waiting for packet to complete...
Waiting for reply...
No reply, is there a listener around?
Receive failed. 33 seconds since last contact.
33 seconds is the longest break in contact so far.
Transmitting...
Sending Hello World #611
Sending...
Waiting for packet to complete...
Waiting for reply...
No reply, is there a listener around?
Receive failed. 35 seconds since last contact.
35 seconds is the longest break in contact so far.
Transmitting...
Sending Hello World #612
Sending...
Waiting for packet to complete...
Waiting for reply...
No reply, is there a listener around?
Receive failed. 37 seconds since last contact.
37 seconds is the longest break in contact so far.
Transmitting...
Sending Hello World #613
Sending...
Waiting for packet to complete...
Waiting for reply...
No reply, is there a listener around?
Receive failed. 39 seconds since last contact.
39 seconds is the longest break in contact so far.
Transmitting...
Sending Hello World #614
Sending...
Waiting for packet to complete...
Waiting for reply...
No reply, is there a listener around?
Receive failed. 41 seconds since last contact.
41 seconds is the longest break in contact so far.
Transmitting...
Sending Hello World #615
Sending...
Waiting for packet to complete...
Waiting for reply...
No reply, is there a listener around?
Receive failed. 43 seconds since last contact.
43 seconds is the longest break in contact so far.
Transmitting...
Sending Hello World #616
Sending...
Waiting for packet to complete...
Waiting for reply...
No reply, is there a listener around?
Receive failed. 45 seconds since last contact.
45 seconds is the longest break in contact so far.
Transmitting...
Sending Hello World #617
Sending...
Waiting for packet to complete...
Waiting for reply...
No reply, is there a listener around?
Receive failed. 47 seconds since last contact.
47 seconds is the longest break in contact so far.
Transmitting...
Sending Hello World #618
Sending...
Waiting for packet to complete...
Waiting for reply...
No reply, is there a listener around?
Receive failed. 49 seconds since last contact.
49 seconds is the longest break in contact so far.
Transmitting...
Sending Hello World #619
Sending...
Waiting for packet to complete...
Waiting for reply...
No reply, is there a listener around?
Receive failed. 51 seconds since last contact.
51 seconds is the longest break in contact so far.
Transmitting...
Sending Hello World #620
Sending...
Waiting for packet to complete...
Waiting for reply...
No reply, is there a listener around?
Receive failed. 53 seconds since last contact.
53 seconds is the longest break in contact so far.
Transmitting...
Sending Hello World #621
Sending...
Waiting for packet to complete...
Waiting for reply...
No reply, is there a listener around?
Receive failed. 55 seconds since last contact.
55 seconds is the longest break in contact so far.
Transmitting...
Sending Hello World #622
Sending...
Waiting for packet to complete...
Waiting for reply...
No reply, is there a listener around?
Receive failed. 58 seconds since last contact.
58 seconds is the longest break in contact so far.
Transmitting...
Sending Hello World #623
Sending...
Waiting for packet to complete...
Waiting for reply...
No reply, is there a listener around?
Receive failed. 1 minute and 0 seconds since last contact.
1 minute and 0 seconds is the longest break in contact so far.
Transmitting...
Sending Hello World #624
Sending...
Waiting for packet to complete...
Waiting for reply...
No reply, is there a listener around?
Receive failed. 1 minute and 2 seconds since last contact.
1 minute and 2 seconds is the longest break in contact so far.
Transmitting...
Sending Hello World #625
Sending...
Waiting for packet to complete...
Waiting for reply...
No reply, is there a listener around?
Receive failed. 1 minute and 4 seconds since last contact.
1 minute and 4 seconds is the longest break in contact so far.
Transmitting...
Sending Hello World #626
Sending...
Waiting for packet to complete...
Waiting for reply...
No reply, is there a listener around?
Receive failed. 1 minute and 6 seconds since last contact.
1 minute and 6 seconds is the longest break in contact so far.
Transmitting...
Sending Hello World #627
Sending...
Waiting for packet to complete...
Waiting for reply...
No reply, is there a listener around?
Receive failed. 1 minute and 8 seconds since last contact.
1 minute and 8 seconds is the longest break in contact so far.
Transmitting...
Sending Hello World #628
Sending...
Waiting for packet to complete...
Waiting for reply...
No reply, is there a listener around?
Receive failed. 1 minute and 10 seconds since last contact.
1 minute and 10 seconds is the longest break in contact so far.
Transmitting...
Sending Hello World #629
Sending...
Waiting for packet to complete...
Waiting for reply...
No reply, is there a listener around?
Receive failed. 1 minute and 12 seconds since last contact.
1 minute and 12 seconds is the longest break in contact so far.
Transmitting...
Sending Hello World #630
Sending...
Waiting for packet to complete...
Waiting for reply...
No reply, is there a listener around?
Receive failed. 1 minute and 14 seconds since last contact.
1 minute and 14 seconds is the longest break in contact so far.
Transmitting...
Sending Hello World #631
Sending...
Waiting for packet to complete...
Waiting for reply...
No reply, is there a listener around?
Receive failed. 1 minute and 16 seconds since last contact.
1 minute and 16 seconds is the longest break in contact so far.
Transmitting...
Sending Hello World #632
Sending...
Waiting for packet to complete...
Waiting for reply...
No reply, is there a listener around?
Receive failed. 1 minute and 18 seconds since last contact.
1 minute and 18 seconds is the longest break in contact so far.
Transmitting...
Sending Hello World #633
Sending...
Waiting for packet to complete...
Waiting for reply...
No reply, is there a listener around?
Receive failed. 1 minute and 20 seconds since last contact.
1 minute and 20 seconds is the longest break in contact so far.
Transmitting...
Sending Hello World #634
Sending...
Waiting for packet to complete...
Waiting for reply...
No reply, is there a listener around?
Receive failed. 1 minute and 22 seconds since last contact.
1 minute and 22 seconds is the longest break in contact so far.
Transmitting...
Sending Hello World #635
Sending...
Waiting for packet to complete...
Waiting for reply...
No reply, is there a listener around?
Receive failed. 1 minute and 25 seconds since last contact.
1 minute and 25 seconds is the longest break in contact so far.
Transmitting...
Sending Hello World #636
Sending...
Waiting for packet to complete...
Waiting for reply...
No reply, is there a listener around?
Receive failed. 1 minute and 27 seconds since last contact.
1 minute and 27 seconds is the longest break in contact so far.
Transmitting...
Sending Hello World #637
Sending...
Waiting for packet to complete...
Waiting for reply...
No reply, is there a listener around?
Receive failed. 1 minute and 29 seconds since last contact.
1 minute and 29 seconds is the longest break in contact so far.
Transmitting...
Sending Hello World #638
Sending...
Waiting for packet to complete...
Waiting for reply...
No reply, is there a listener around?
Receive failed. 1 minute and 31 seconds since last contact.
1 minute and 31 seconds is the longest break in contact so far.
Transmitting...
Sending Hello World #639
Sending...
Waiting for packet to complete...
Waiting for reply...
No reply, is there a listener around?
Receive failed. 1 minute and 33 seconds since last contact.
1 minute and 33 seconds is the longest break in contact so far.
Transmitting...
Sending Hello World #640
Sending...
Waiting for packet to complete...
Waiting for reply...
No reply, is there a listener around?
Receive failed. 1 minute and 35 seconds since last contact.
1 minute and 35 seconds is the longest break in contact so far.
Transmitting...
Sending Hello World #641
Sending...
Waiting for packet to complete...
Waiting for reply...
No reply, is there a listener around?
Receive failed. 1 minute and 37 seconds since last contact.
1 minute and 37 seconds is the longest break in contact so far.
Transmitting...
Sending Hello World #642
Sending...
Waiting for packet to complete...
Waiting for reply...
No reply, is there a listener around?
Receive failed. 1 minute and 39 seconds since last contact.
1 minute and 39 seconds is the longest break in contact so far.
Transmitting...
Sending Hello World #643
Sending...
Waiting for packet to complete...
Waiting for reply...
No reply, is there a listener around?
Receive failed. 1 minute and 41 seconds since last contact.
1 minute and 41 seconds is the longest break in contact so far.
Transmitting...
Sending Hello World #644
Sending...
Waiting for packet to complete...
Waiting for reply...
No reply, is there a listener around?
Receive failed. 1 minute and 43 seconds since last contact.
1 minute and 43 seconds is the longest break in contact so far.
Transmitting...
Sending Hello World #645
Sending...
Waiting for packet to complete...
Waiting for reply...
No reply, is there a listener around?
Receive failed. 1 minute and 45 seconds since last contact.
1 minute and 45 seconds is the longest break in contact so far.
Transmitting...
Sending Hello World #646
Sending...
Waiting for packet to complete...
Waiting for reply...
No reply, is there a listener around?
Receive failed. 1 minute and 47 seconds since last contact.
1 minute and 47 seconds is the longest break in contact so far.
Transmitting...
Sending Hello World #647
Sending...
Waiting for packet to complete...
Waiting for reply...
No reply, is there a listener around?
Receive failed. 1 minute and 49 seconds since last contact.
1 minute and 49 seconds is the longest break in contact so far.
Transmitting...
Sending Hello World #648
Sending...
Waiting for packet to complete...
Waiting for reply...
No reply, is there a listener around?
Receive failed. 1 minute and 51 seconds since last contact.
1 minute and 51 seconds is the longest break in contact so far.
Transmitting...
Sending Hello World #649
Sending...
Waiting for packet to complete...
Waiting for reply...
No reply, is there a listener around?
Receive failed. 1 minute and 54 seconds since last contact.
1 minute and 54 seconds is the longest break in contact so far.
Transmitting...
Sending Hello World #650
Sending...
Waiting for packet to complete...
Waiting for reply...
No reply, is there a listener around?
Receive failed. 1 minute and 56 seconds since last contact.
1 minute and 56 seconds is the longest break in contact so far.
Transmitting...
Sending Hello World #651
Sending...
Waiting for packet to complete...
Waiting for reply...
No reply, is there a listener around?
Receive failed. 1 minute and 58 seconds since last contact.
1 minute and 58 seconds is the longest break in contact so far.
Transmitting...
Sending Hello World #652
Sending...
Waiting for packet to complete...
Waiting for reply...
No reply, is there a listener around?
Receive failed. 2 minutes and 0 seconds since last contact.
2 minutes and 0 seconds is the longest break in contact so far.
Transmitting...
Sending Hello World #653
Sending...
Waiting for packet to complete...
Waiting for reply...
No reply, is there a listener around?
Receive failed. 2 minutes and 2 seconds since last contact.
2 minutes and 2 seconds is the longest break in contact so far.
Transmitting...
Sending Hello World #654
Sending...
Waiting for packet to complete...
Waiting for reply...
No reply, is there a listener around?
Receive failed. 2 minutes and 4 seconds since last contact.
2 minutes and 4 seconds is the longest break in contact so far.
Transmitting...
Sending Hello World #655
Sending...
Waiting for packet to complete...
Waiting for reply...
No reply, is there a listener around?
Receive failed. 2 minutes and 6 seconds since last contact.
2 minutes and 6 seconds is the longest break in contact so far.
Transmitting...
Sending Hello World #656
Sending...
Waiting for packet to complete...
Waiting for reply...
Got reply: And hello back to you
RSSI: -53
2 minutes and 6 seconds is the longest break in contact so far.
Transmitting...
Sending Hello World #657
Sending...
Waiting for packet to complete...
Waiting for reply...
No reply, is there a listener around?
Receive failed. 2 seconds since last contact.
2 minutes and 6 seconds is the longest break in contact so far.
Transmitting...
Sending Hello World #658
Sending...
Waiting for packet to complete...
Waiting for reply...
Got reply: And hello back to you
RSSI: -57
2 minutes and 6 seconds is the longest break in contact so far.
Transmitting...
Sending Hello World #659
Sending...
Waiting for packet to complete...
Waiting for reply...
Got reply: And hello back to you
RSSI: -61
2 minutes and 6 seconds is the longest break in contact so far.
Transmitting...
Sending Hello World #660
Sending...
Waiting for packet to complete...
Waiting for reply...
No reply, is there a listener around?
Receive failed. 2 seconds since last contact.
2 minutes and 6 seconds is the longest break in contact so far.
Transmitting...
Sending Hello World #661
Sending...
Waiting for packet to complete...
Waiting for reply...
Got reply: And hello back to you
RSSI: -58
2 minutes and 6 seconds is the longest break in contact so far.
Transmitting...
Sending Hello World #662
Sending...
Waiting for packet to complete...
Waiting for reply...
Got reply: And hello back to you
RSSI: -58
2 minutes and 6 seconds is the longest break in contact so far.
Transmitting...
Sending Hello World #663
Sending...
Waiting for packet to complete...
Waiting for reply...
Got reply: And hello back to you
RSSI: -58
2 minutes and 6 seconds is the longest break in contact so far.
Transmitting...
Sending Hello World #664
Sending...
Waiting for packet to complete...
Waiting for reply...
Got reply: And hello back to you
RSSI: -59
2 minutes and 6 seconds is the longest break in contact so far.
Transmitting...
Sending Hello World #665
Sending...
Waiting for packet to complete...
Waiting for reply...
Got reply: And hello back to you
RSSI: -58
2 minutes and 6 seconds is the longest break in contact so far.
Transmitting...
Sending Hello World #666
Sending...
Waiting for packet to complete...
Waiting for reply...
Got reply: And hello back to you
RSSI: -54
2 minutes and 6 seconds is the longest break in contact so far.
Transmitting...
Sending Hello World #667
Sending...
Waiting for packet to complete...
Waiting for reply...
Got reply: And hello back to you
RSSI: -57
2 minutes and 6 seconds is the longest break in contact so far.
Transmitting...
Sending Hello World #668
Sending...
Waiting for packet to complete...
Waiting for reply...
Got reply: And hello back to you
RSSI: -54
2 minutes and 6 seconds is the longest break in contact so far.
Transmitting...
Sending Hello World #669
Sending...
Waiting for packet to complete...
Waiting for reply...
Got reply: And hello back to you
RSSI: -52
2 minutes and 6 seconds is the longest break in contact so far.
Transmitting...
Sending Hello World #670
Sending...
Waiting for packet to complete...
Waiting for reply...
Got reply: And hello back to you
RSSI: -55
2 minutes and 6 seconds is the longest break in contact so far.
Transmitting...
Sending Hello World #671
Sending...
Waiting for packet to complete...
Waiting for reply...
Got reply: And hello back to you
RSSI: -51
2 minutes and 6 seconds is the longest break in contact so far.
Transmitting...
Sending Hello World #672
Sending...
Waiting for packet to complete...
Waiting for reply...
Got reply: And hello back to you
RSSI: -52
2 minutes and 6 seconds is the longest break in contact so far.
Transmitting...
Sending Hello World #673
Sending...
Waiting for packet to complete...
Waiting for reply...
Got reply: And hello back to you
RSSI: -54
2 minutes and 6 seconds is the longest break in contact so far.
Transmitting...
Sending Hello World #674
Sending...
Waiting for packet to complete...
Waiting for reply...
Got reply: And hello back to you
RSSI: -58
2 minutes and 6 seconds is the longest break in contact so far.
Transmitting...
Sending Hello World #675
Sending...
Waiting for packet to complete...
Waiting for reply...
Got reply: And hello back to you
RSSI: -56
2 minutes and 6 seconds is the longest break in contact so far.
Transmitting...
Sending Hello World #676
Sending...
Waiting for packet to complete...
Waiting for reply...
Got reply: And hello back to you
RSSI: -58
2 minutes and 6 seconds is the longest break in contact so far.
Transmitting...
Sending Hello World #677
Sending...
Waiting for packet to complete...
Waiting for reply...
Got reply: And hello back to you
RSSI: -58
2 minutes and 6 seconds is the longest break in contact so far.
Transmitting...
Sending Hello World #678
Sending...
Waiting for packet to complete...
Waiting for reply...
Got reply: And hello back to you
RSSI: -57
2 minutes and 6 seconds is the longest break in contact so far.
Transmitting...
Sending Hello World #679
Sending...
Waiting for packet to complete...
Waiting for reply...
Got reply: And hello back to you
RSSI: -59
2 minutes and 6 seconds is the longest break in contact so far.
Transmitting...
Sending Hello World #680
Sending...
Waiting for packet to complete...
Waiting for reply...
Got reply: And hello back to you
RSSI: -57
2 minutes and 6 seconds is the longest break in contact so far.
Transmitting...
Sending Hello World #681
Sending...
Waiting for packet to complete...
Waiting for reply...
Got reply: And hello back to you
RSSI: -56
2 minutes and 6 seconds is the longest break in contact so far.
Transmitting...
Sending Hello World #682
Sending...
Waiting for packet to complete...
Waiting for reply...
Got reply: And hello back to you
RSSI: -52
2 minutes and 6 seconds is the longest break in contact so far.
Transmitting...
Sending Hello World #683
Sending...
Waiting for packet to complete...
Waiting for reply...
Got reply: And hello back to you
RSSI: -52
2 minutes and 6 seconds is the longest break in contact so far.
Transmitting...
Sending Hello World #684
Sending...
Waiting for packet to complete...
Waiting for reply...
Got reply: And hello back to you
RSSI: -54
2 minutes and 6 seconds is the longest break in contact so far.
Transmitting...
Sending Hello World #685
Sending...
Waiting for packet to complete...
Waiting for reply...
Got reply: And hello back to you
RSSI: -53
2 minutes and 6 seconds is the longest break in contact so far.
Transmitting...
Sending Hello World #686
Sending...
Waiting for packet to complete...
Waiting for reply...
No reply, is there a listener around?
Receive failed. 2 seconds since last contact.
2 minutes and 6 seconds is the longest break in contact so far.
Transmitting...
Sending Hello World #687
Sending...
Waiting for packet to complete...
Waiting for reply...
Got reply: And hello back to you
RSSI: -52
2 minutes and 6 seconds is the longest break in contact so far.
Transmitting...
Sending Hello World #688
Sending...
Waiting for packet to complete...
Waiting for reply...
Got reply: And hello back to you
RSSI: -52
2 minutes and 6 seconds is the longest break in contact so far.
Transmitting...
Sending Hello World #689
Sending...
Waiting for packet to complete...
Waiting for reply...
Got reply: And hello back to you
RSSI: -52
2 minutes and 6 seconds is the longest break in contact so far.
Transmitting...
Sending Hello World #690
Sending...
Waiting for packet to complete...
Waiting for reply...
Got reply: And hello back to you
RSSI: -52
2 minutes and 6 seconds is the longest break in contact so far.
Transmitting...
Sending Hello World #691
Sending...
Waiting for packet to complete...
Waiting for reply...
Got reply: And hello back to you
RSSI: -52
2 minutes and 6 seconds is the longest break in contact so far.
Transmitting...
Sending Hello World #692
Sending...
Waiting for packet to complete...
Waiting for reply...
Got reply: And hello back to you
RSSI: -51
2 minutes and 6 seconds is the longest break in contact so far.
Transmitting...
Sending Hello World #693
Sending...
Waiting for packet to complete...
Waiting for reply...
Got reply: And hello back to you
RSSI: -53
2 minutes and 6 seconds is the longest break in contact so far.
Transmitting...
Sending Hello World #694
Sending...
Waiting for packet to complete...
Waiting for reply...
Got reply: And hello back to you
RSSI: -52
2 minutes and 6 seconds is the longest break in contact so far.
Transmitting...
Sending Hello World #695
Sending...
Waiting for packet to complete...
Waiting for reply...
Got reply: And hello back to you
RSSI: -53
2 minutes and 6 seconds is the longest break in contact so far.
Transmitting...
Sending Hello World #696
Sending...
Waiting for packet to complete...
Waiting for reply...
Got reply: And hello back to you
RSSI: -53
2 minutes and 6 seconds is the longest break in contact so far.
Transmitting...
Sending Hello World #697
Sending...
Waiting for packet to complete...
Waiting for reply...
Got reply: And hello back to you
RSSI: -53
2 minutes and 6 seconds is the longest break in contact so far.
Transmitting...
Sending Hello World #698
Sending...
Waiting for packet to complete...
Waiting for reply...
Got reply: And hello back to you
RSSI: -53
2 minutes and 6 seconds is the longest break in contact so far.
Transmitting...
Sending Hello World #699
Sending...
Waiting for packet to complete...
Waiting for reply...
No reply, is there a listener around?
Receive failed. 2 seconds since last contact.
2 minutes and 6 seconds is the longest break in contact so far.
Transmitting...
Sending Hello World #700
Sending...
Waiting for packet to complete...
Waiting for reply...
Got reply: And hello back to you
RSSI: -52
2 minutes and 6 seconds is the longest break in contact so far.
Transmitting...
Sending Hello World #701
Sending...
Waiting for packet to complete...
Waiting for reply...
Got reply: And hello back to you
RSSI: -54
2 minutes and 6 seconds is the longest break in contact so far.
Transmitting...
Sending Hello World #702
Sending...
Waiting for packet to complete...
Waiting for reply...
Got reply: And hello back to you
RSSI: -56
2 minutes and 6 seconds is the longest break in contact so far.
Transmitting...
Sending Hello World #703
Sending...
Waiting for packet to complete...
Waiting for reply...
Got reply: And hello back to you
RSSI: -55
2 minutes and 6 seconds is the longest break in contact so far.
Transmitting...
Sending Hello World #704
Sending...
Waiting for packet to complete...
Waiting for reply...
Got reply: And hello back to you
RSSI: -54
2 minutes and 6 seconds is the longest break in contact so far.
Transmitting...
Sending Hello World #705
Sending...
Waiting for packet to complete...
Waiting for reply...
Got reply: And hello back to you
RSSI: -53
2 minutes and 6 seconds is the longest break in contact so far.
Transmitting...
Sending Hello World #706
Sending...
Waiting for packet to complete...
Waiting for reply...
No reply, is there a listener around?
Receive failed. 2 seconds since last contact.
2 minutes and 6 seconds is the longest break in contact so far.
Transmitting...
Sending Hello World #707
Sending...
Waiting for packet to complete...
Waiting for reply...
Got reply: And hello back to you
RSSI: -54
2 minutes and 6 seconds is the longest break in contact so far.
Transmitting...
Sending Hello World #708
Sending...
Waiting for packet to complete...
Waiting for reply...
Got reply: And hello back to you
RSSI: -55
2 minutes and 6 seconds is the longest break in contact so far.
Transmitting...
Sending Hello World #709
Sending...
Waiting for packet to complete...
Waiting for reply...
Got reply: And hello back to you
RSSI: -55
2 minutes and 6 seconds is the longest break in contact so far.
Transmitting...
Sending Hello World #710
Sending...
Waiting for packet to complete...
Waiting for reply...
Got reply: And hello back to you
RSSI: -55
2 minutes and 6 seconds is the longest break in contact so far.
Transmitting...
Sending Hello World #711
Sending...
Waiting for packet to complete...
Waiting for reply...
Got reply: And hello back to you
RSSI: -54
2 minutes and 6 seconds is the longest break in contact so far.
Transmitting...
Sending Hello World #712
Sending...
Waiting for packet to complete...
Waiting for reply...
Got reply: And hello back to you
RSSI: -54
2 minutes and 6 seconds is the longest break in contact so far.
Transmitting...
Sending Hello World #713
Sending...
Waiting for packet to complete...
Waiting for reply...
Got reply: And hello back to you
RSSI: -54
2 minutes and 6 seconds is the longest break in contact so far.
Transmitting...
Sending Hello World #714
Sending...
Waiting for packet to complete...
Waiting for reply...
Got reply: And hello back to you
RSSI: -54
2 minutes and 6 seconds is the longest break in contact so far.
Transmitting...
Sending Hello World #715
Sending...
Waiting for packet to complete...
Waiting for reply...
Got reply: And hello back to you
RSSI: -53
2 minutes and 6 seconds is the longest break in contact so far.
Transmitting...
Sending Hello World #716
Sending...
Waiting for packet to complete...
Waiting for reply...
Got reply: And hello back to you
RSSI: -54
2 minutes and 6 seconds is the longest break in contact so far.
Transmitting...
Sending Hello World #717
Sending...
Waiting for packet to complete...
Waiting for reply...
Got reply: And hello back to you
RSSI: -54
2 minutes and 6 seconds is the longest break in contact so far.
Transmitting...
Sending Hello World #718
Sending...
Waiting for packet to complete...
Waiting for reply...
Got reply: And hello back to you
RSSI: -54
2 minutes and 6 seconds is the longest break in contact so far.
Transmitting...
Sending Hello World #719
Sending...
Waiting for packet to complete...
Waiting for reply...
Got reply: And hello back to you
RSSI: -54
2 minutes and 6 seconds is the longest break in contact so far.
Transmitting...
Sending Hello World #720
Sending...
Waiting for packet to complete...
Waiting for reply...
Got reply: And hello back to you
RSSI: -57
2 minutes and 6 seconds is the longest break in contact so far.
Transmitting...
Sending Hello World #721
Sending...
Waiting for packet to complete...
Waiting for reply...
Got reply: And hello back to you
RSSI: -54
2 minutes and 6 seconds is the longest break in contact so far.
Transmitting...
Sending Hello World #722
Sending...
Waiting for packet to complete...
Waiting for reply...
Got reply: And hello back to you
RSSI: -60
2 minutes and 6 seconds is the longest break in contact so far.
Transmitting...
Sending Hello World #723
Sending...
Waiting for packet to complete...
Waiting for reply...
Got reply: And hello back to you
RSSI: -54
2 minutes and 6 seconds is the longest break in contact so far.
Transmitting...
Sending Hello World #724
Sending...
Waiting for packet to complete...
Waiting for reply...
Got reply: And hello back to you
RSSI: -53
2 minutes and 6 seconds is the longest break in contact so far.
Transmitting...
Sending Hello World #725
Sending...
Waiting for packet to complete...
Waiting for reply...
Got reply: And hello back to you
RSSI: -55
2 minutes and 6 seconds is the longest break in contact so far.
Transmitting...
Sending Hello World #726
Sending...
Waiting for packet to complete...
Waiting for reply...
Got reply: And hello back to you
RSSI: -54
2 minutes and 6 seconds is the longest break in contact so far.
Transmitting...
Sending Hello World #727
Sending...
Waiting for packet to complete...
Waiting for reply...
Got reply: And hello back to you
RSSI: -55
2 minutes and 6 seconds is the longest break in contact so far.
Transmitting...
Sending Hello World #728
Sending...
Waiting for packet to complete...
Waiting for reply...
Got reply: And hello back to you
RSSI: -54
2 minutes and 6 seconds is the longest break in contact so far.
Transmitting...
Sending Hello World #729
Sending...
Waiting for packet to complete...
Waiting for reply...
Got reply: And hello back to you
RSSI: -55
2 minutes and 6 seconds is the longest break in contact so far.
Transmitting...
Sending Hello World #730
Sending...
Waiting for packet to complete...
Waiting for reply...
No reply, is there a listener around?
Receive failed. 2 seconds since last contact.
2 minutes and 6 seconds is the longest break in contact so far.
Transmitting...
Sending Hello World #731
Sending...
Waiting for packet to complete...
Waiting for reply...
Got reply: And hello back to you
RSSI: -55
2 minutes and 6 seconds is the longest break in contact so far.
Transmitting...
Sending Hello World #732
Sending...
Waiting for packet to complete...
Waiting for reply...
Got reply: And hello back to you
RSSI: -55
2 minutes and 6 seconds is the longest break in contact so far.
Transmitting...
Sending Hello World #733
Sending...
Waiting for packet to complete...
Waiting for reply...
Got reply: And hello back to you
RSSI: -55
2 minutes and 6 seconds is the longest break in contact so far.
Transmitting...
Sending Hello World #734
Sending...
Waiting for packet to complete...
Waiting for reply...
Got reply: And hello back to you
RSSI: -55
2 minutes and 6 seconds is the longest break in contact so far.
Transmitting...
Sending Hello World #735
Sending...
Waiting for packet to complete...
Waiting for reply...
Got reply: And hello back to you
RSSI: -53
2 minutes and 6 seconds is the longest break in contact so far.
Transmitting...
Sending Hello World #736
Sending...
Waiting for packet to complete...
Waiting for reply...
Got reply: And hello back to you
RSSI: -51
2 minutes and 6 seconds is the longest break in contact so far.
Transmitting...
Sending Hello World #737
Sending...
Waiting for packet to complete...
Waiting for reply...
Got reply: And hello back to you
RSSI: -55
2 minutes and 6 seconds is the longest break in contact so far.
Transmitting...
Sending Hello World #738
Sending...
Waiting for packet to complete...
Waiting for reply...
Got reply: And hello back to you
RSSI: -54
2 minutes and 6 seconds is the longest break in contact so far.
Transmitting...
Sending Hello World #739
Sending...
Waiting for packet to complete...
Waiting for reply...
Got reply: And hello back to you
RSSI: -53
2 minutes and 6 seconds is the longest break in contact so far.
Transmitting...
Sending Hello World #740
Sending...
Waiting for packet to complete...
Waiting for reply...
Got reply: And hello back to you
RSSI: -53
2 minutes and 6 seconds is the longest break in contact so far.
Transmitting...
Sending Hello World #741
Sending...
Waiting for packet to complete...
Waiting for reply...
Got reply: And hello back to you
RSSI: -53
2 minutes and 6 seconds is the longest break in contact so far.
Transmitting...
Sending Hello World #742
Sending...
Waiting for packet to complete...
Waiting for reply...
Got reply: And hello back to you
RSSI: -55
2 minutes and 6 seconds is the longest break in contact so far.
Transmitting...
Sending Hello World #743
Sending...
Waiting for packet to complete...
Waiting for reply...
Got reply: And hello back to you
RSSI: -55
2 minutes and 6 seconds is the longest break in contact so far.
Transmitting...
Sending Hello World #744
Sending...
Waiting for packet to complete...
Waiting for reply...
Got reply: And hello back to you
RSSI: -53
2 minutes and 6 seconds is the longest break in contact so far.
Transmitting...
Sending Hello World #745
Sending...
Waiting for packet to complete...
Waiting for reply...
Got reply: And hello back to you
RSSI: -53
2 minutes and 6 seconds is the longest break in contact so far.
Transmitting...
Sending Hello World #746
Sending...
Waiting for packet to complete...
Waiting for reply...
Got reply: And hello back to you
RSSI: -53
2 minutes and 6 seconds is the longest break in contact so far.
Transmitting...
Sending Hello World #747
Sending...
Waiting for packet to complete...
Waiting for reply...
Got reply: And hello back to you
RSSI: -54
2 minutes and 6 seconds is the longest break in contact so far.
Transmitting...
Sending Hello World #748
Sending...
Waiting for packet to complete...
Waiting for reply...
Got reply: And hello back to you
RSSI: -54
2 minutes and 6 seconds is the longest break in contact so far.
Transmitting...
Sending Hello World #749
Sending...
Waiting for packet to complete...
Waiting for reply...
Got reply: And hello back to you
RSSI: -54
2 minutes and 6 seconds is the longest break in contact so far.
Transmitting...
Sending Hello World #750
Sending...
Waiting for packet to complete...
Waiting for reply...
Got reply: And hello back to you
RSSI: -52
2 minutes and 6 seconds is the longest break in contact so far.
Transmitting...
Sending Hello World #751
Sending...
Waiting for packet to complete...
Waiting for reply...
Got reply: And hello back to you
RSSI: -54
2 minutes and 6 seconds is the longest break in contact so far.
Transmitting...
Sending Hello World #752
Sending...
Waiting for packet to complete...
Waiting for reply...
Got reply: And hello back to you
RSSI: -52
2 minutes and 6 seconds is the longest break in contact so far.
Transmitting...
Sending Hello World #753
Sending...
Waiting for packet to complete...
Waiting for reply...
Got reply: And hello back to you
RSSI: -52
2 minutes and 6 seconds is the longest break in contact so far.
Transmitting...
Sending Hello World #754
Sending...
Waiting for packet to complete...
Waiting for reply...
Got reply: And hello back to you
RSSI: -58
2 minutes and 6 seconds is the longest break in contact so far.
Transmitting...
Sending Hello World #755
Sending...
Waiting for packet to complete...
Waiting for reply...
Got reply: And hello back to you
RSSI: -60
2 minutes and 6 seconds is the longest break in contact so far.
Transmitting...
Sending Hello World #756
Sending...
Waiting for packet to complete...
Waiting for reply...
Got reply: And hello back to you
RSSI: -61
2 minutes and 6 seconds is the longest break in contact so far.
Transmitting...
Sending Hello World #757
Sending...
Waiting for packet to complete...
Waiting for reply...
Got reply: And hello back to you
RSSI: -61
2 minutes and 6 seconds is the longest break in contact so far.
Transmitting...
Sending Hello World #758
Sending...
Waiting for packet to complete...
Waiting for reply...
Got reply: And hello back to you
RSSI: -54
2 minutes and 6 seconds is the longest break in contact so far.
Transmitting...
Sending Hello World #759
Sending...
Waiting for packet to complete...
Waiting for reply...
Got reply: And hello back to you
RSSI: -52
2 minutes and 6 seconds is the longest break in contact so far.
Transmitting...
Sending Hello World #760
Sending...
Waiting for packet to complete...
Waiting for reply...
Got reply: And hello back to you
RSSI: -51
2 minutes and 6 seconds is the longest break in contact so far.
Transmitting...
Sending Hello World #761
Sending...
Waiting for packet to complete...
Waiting for reply...
Got reply: And hello back to you
RSSI: -52
2 minutes and 6 seconds is the longest break in contact so far.
Transmitting...
Sending Hello World #762
Sending...
Waiting for packet to complete...
Waiting for reply...
Got reply: And hello back to you
RSSI: -53
2 minutes and 6 seconds is the longest break in contact so far.
Transmitting...
Sending Hello World #763
Sending...
Waiting for packet to complete...
Waiting for reply...
Got reply: And hello back to you
RSSI: -52
2 minutes and 6 seconds is the longest break in contact so far.
Transmitting...
Sending Hello World #764
Sending...
Waiting for packet to complete...
Waiting for reply...
Got reply: And hello back to you
RSSI: -52
2 minutes and 6 seconds is the longest break in contact so far.
Transmitting...
Sending Hello World #765
Sending...
Waiting for packet to complete...
Waiting for reply...
Got reply: And hello back to you
RSSI: -52
2 minutes and 6 seconds is the longest break in contact so far.
Transmitting...
Sending Hello World #766
Sending...
Waiting for packet to complete...
Waiting for reply...
Got reply: And hello back to you
RSSI: -52
2 minutes and 6 seconds is the longest break in contact so far.
Transmitting...
Sending Hello World #767
Sending...
Waiting for packet to complete...
Waiting for reply...
Got reply: And hello back to you
RSSI: -52
2 minutes and 6 seconds is the longest break in contact so far.
Transmitting...
Sending Hello World #768
Sending...
Waiting for packet to complete...
Waiting for reply...
Got reply: And hello back to you
RSSI: -52
2 minutes and 6 seconds is the longest break in contact so far.
Transmitting...
Sending Hello World #769
Sending...
Waiting for packet to complete...
Waiting for reply...
Got reply: And hello back to you
RSSI: -51
2 minutes and 6 seconds is the longest break in contact so far.
Transmitting...
Sending Hello World #770
Sending...
Waiting for packet to complete...
Waiting for reply...
Got reply: And hello back to you
RSSI: -51
2 minutes and 6 seconds is the longest break in contact so far.
Transmitting...
Sending Hello World #771
Sending...
Waiting for packet to complete...
Waiting for reply...
Got reply: And hello back to you
RSSI: -51
2 minutes and 6 seconds is the longest break in contact so far.
Transmitting...
Sending Hello World #772
Sending...
Waiting for packet to complete...
Waiting for reply...
Got reply: And hello back to you
RSSI: -51
2 minutes and 6 seconds is the longest break in contact so far.
Transmitting...
Sending Hello World #773
Sending...
Waiting for packet to complete...
Waiting for reply...
Got reply: And hello back to you
RSSI: -52
2 minutes and 6 seconds is the longest break in contact so far.
Transmitting...
Sending Hello World #774
Sending...
Waiting for packet to complete...
Waiting for reply...
Got reply: And hello back to you
RSSI: -52
2 minutes and 6 seconds is the longest break in contact so far.
Transmitting...
Sending Hello World #775
Sending...
Waiting for packet to complete...
Waiting for reply...
Got reply: And hello back to you
RSSI: -53
2 minutes and 6 seconds is the longest break in contact so far.
Transmitting...
Sending Hello World #776
Sending...
Waiting for packet to complete...
Waiting for reply...
Got reply: And hello back to you
RSSI: -54
2 minutes and 6 seconds is the longest break in contact so far.
Transmitting...
Sending Hello World #777
Sending...
Waiting for packet to complete...
Waiting for reply...
Got reply: And hello back to you
RSSI: -57
2 minutes and 6 seconds is the longest break in contact so far.
Transmitting...
Sending Hello World #778
Sending...
Waiting for packet to complete...
Waiting for reply...
No reply, is there a listener around?
Receive failed. 2 seconds since last contact.
2 minutes and 6 seconds is the longest break in contact so far.
Transmitting...
Sending Hello World #779
Sending...
Waiting for packet to complete...
Waiting for reply...
Got reply: And hello back to you
RSSI: -57
2 minutes and 6 seconds is the longest break in contact so far.
Transmitting...
Sending Hello World #780
Sending...
Waiting for packet to complete...
Waiting for reply...
Got reply: And hello back to you
RSSI: -57
2 minutes and 6 seconds is the longest break in contact so far.
Transmitting...
Sending Hello World #781
Sending...
Waiting for packet to complete...
Waiting for reply...
Got reply: And hello back to you
RSSI: -57
2 minutes and 6 seconds is the longest break in contact so far.
Transmitting...
Sending Hello World #782
Sending...
Waiting for packet to complete...
Waiting for reply...
Got reply: And hello back to you
RSSI: -58
2 minutes and 6 seconds is the longest break in contact so far.
Transmitting...
Sending Hello World #783
Sending...
Waiting for packet to complete...
Waiting for reply...
Got reply: And hello back to you
RSSI: -58
2 minutes and 6 seconds is the longest break in contact so far.
Transmitting...
Sending Hello World #784
Sending...
Waiting for packet to complete...
Waiting for reply...
Got reply: And hello back to you
RSSI: -63
2 minutes and 6 seconds is the longest break in contact so far.
Transmitting...
Sending Hello World #785
Sending...
Waiting for packet to complete...
Waiting for reply...
Got reply: And hello back to you
RSSI: -57
2 minutes and 6 seconds is the longest break in contact so far.
Transmitting...
Sending Hello World #786
Sending...
Waiting for packet to complete...
Waiting for reply...
Got reply: And hello back to you
RSSI: -55
2 minutes and 6 seconds is the longest break in contact so far.
Transmitting...
Sending Hello World #787
Sending...
Waiting for packet to complete...
Waiting for reply...
Got reply: And hello back to you
RSSI: -56
2 minutes and 6 seconds is the longest break in contact so far.
Transmitting...
Sending Hello World #788
Sending...
Waiting for packet to complete...
Waiting for reply...
Got reply: And hello back to you
RSSI: -57
2 minutes and 6 seconds is the longest break in contact so far.
Transmitting...
Sending Hello World #789
Sending...
Waiting for packet to complete...
Waiting for reply...
Got reply: And hello back to you
RSSI: -55
2 minutes and 6 seconds is the longest break in contact so far.
Transmitting...
Sending Hello World #790
Sending...
Waiting for packet to complete...
Waiting for reply...
Got reply: And hello back to you
RSSI: -54
2 minutes and 6 seconds is the longest break in contact so far.
Transmitting...
Sending Hello World #791
Sending...
Waiting for packet to complete...
Waiting for reply...
Got reply: And hello back to you
RSSI: -55
2 minutes and 6 seconds is the longest break in contact so far.
Transmitting...
Sending Hello World #792
Sending...
Waiting for packet to complete...
Waiting for reply...
Got reply: And hello back to you
RSSI: -53
2 minutes and 6 seconds is the longest break in contact so far.
Transmitting...
Sending Hello World #793
Sending...
Waiting for packet to complete...
Waiting for reply...
Got reply: And hello back to you
RSSI: -56
2 minutes and 6 seconds is the longest break in contact so far.
Transmitting...
Sending Hello World #794
Sending...
Waiting for packet to complete...
Waiting for reply...
Got reply: And hello back to you
RSSI: -56
2 minutes and 6 seconds is the longest break in contact so far.
Transmitting...
Sending Hello World #795
Sending...
Waiting for packet to complete...
Waiting for reply...
Got reply: And hello back to you
RSSI: -56
2 minutes and 6 seconds is the longest break in contact so far.
Transmitting...
Sending Hello World #796
Sending...
Waiting for packet to complete...
Waiting for reply...
Got reply: And hello back to you
RSSI: -58
2 minutes and 6 seconds is the longest break in contact so far.
Transmitting...
Sending Hello World #797
Sending...
Waiting for packet to complete...
Waiting for reply...
Got reply: And hello back to you
RSSI: -53
2 minutes and 6 seconds is the longest break in contact so far.
Transmitting...
Sending Hello World #798
Sending...
Waiting for packet to complete...
Waiting for reply...
Got reply: And hello back to you
RSSI: -51
2 minutes and 6 seconds is the longest break in contact so far.
Transmitting...
Se9nding Hello World #799
Sending...
Waiting for packet to complete...
Waiting for reply...
Got reply: And hello back to you
RSSI: -53
2 minutes and 6 seconds is the longest break in contact so far.
Transmitting...
Sending Hello World #800
Sending...
Waiting for packet to complete...
Waiting for reply...
Got reply: And hello back to you
RSSI: -52
2 minutes and 6 seconds is the longest break in contact so far.
Transmitting...
Sending Hello World #801
Sending...
Waiting for packet to complete...
Waiting for reply...
Got reply: And hello back to you
RSSI: -55
2 minutes and 6 seconds is the longest break in contact so far.
Transmitting...
Sending Hello World #802
Sending...
Waiting for packet to complete...
Waiting for reply...
Got reply: And hello back to you
RSSI: -53
2 minutes and 6 seconds is the longest break in contact so far.
Transmitting...
Sending Hello World #803
Sending...
Waiting for packet to complete...
Waiting for reply...
Got reply: And hello back to you
RSSI: -56
2 minutes and 6 seconds is the longest break in contact so far.
T

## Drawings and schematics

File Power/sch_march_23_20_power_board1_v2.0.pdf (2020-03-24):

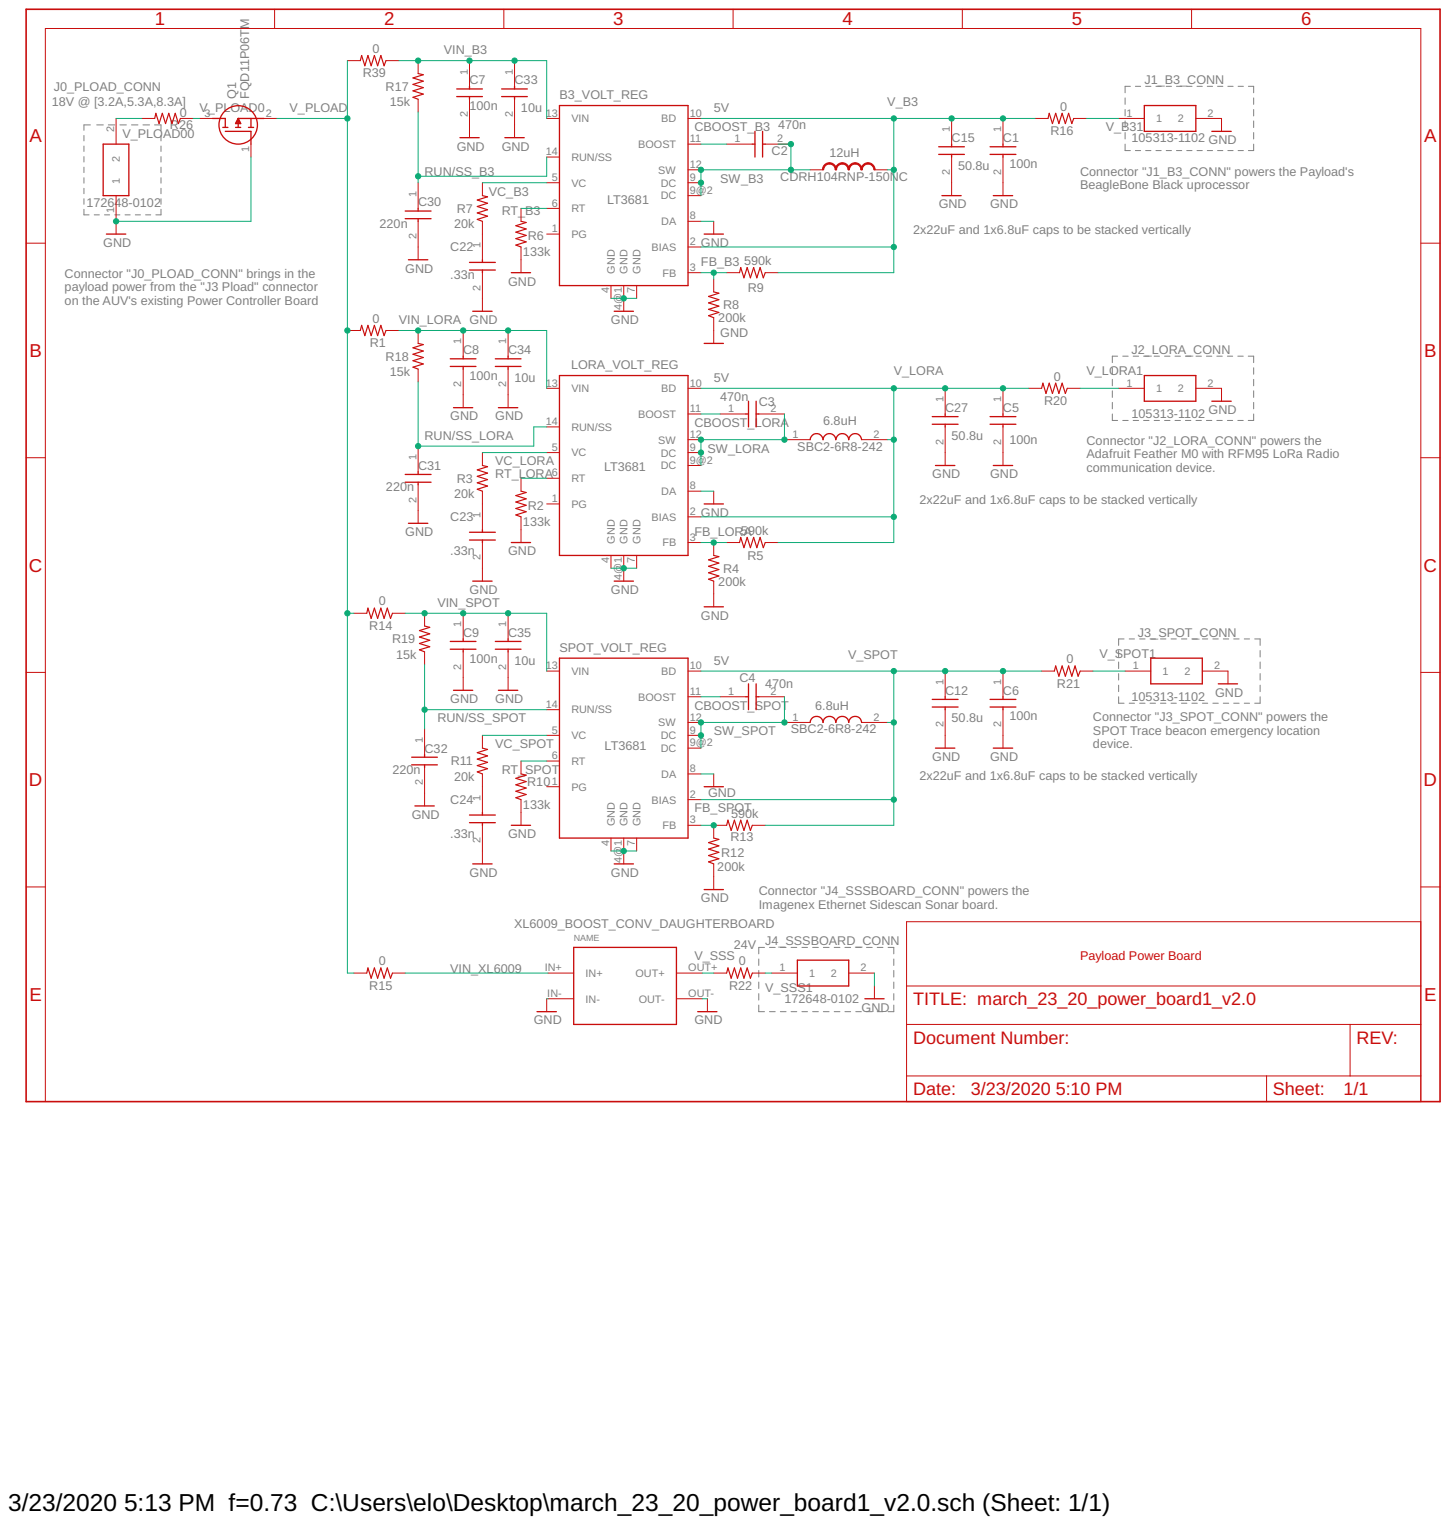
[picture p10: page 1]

Connector "J1_B3_CONN" powers the Payload's BeagleBone Black uprocessor

2x22uF and 1x6.8uF caps to be stacked vertically

Connector "J0_PLOAD_CONN" brings in the
payload power from the "J3 Pload" connector on the AUV's existing Power Controller Board

Connector "J2_LORA_CONN" powers the Adafruit Feather M0 with RFM95 LoRa Radio

Connector "J3_SPOT_CONN" powers the SPOT Trace beacon emergency location

Connector "J4_SSSBOARD_CONN" powers the
Imagenex Ethernet Sidescan Sonar board.

3/23/2020 5:13 PM f=0.73 C:\Users\elo\Desktop\march_23_20_power_board1_v2.0.sch (Sheet: 1/1)

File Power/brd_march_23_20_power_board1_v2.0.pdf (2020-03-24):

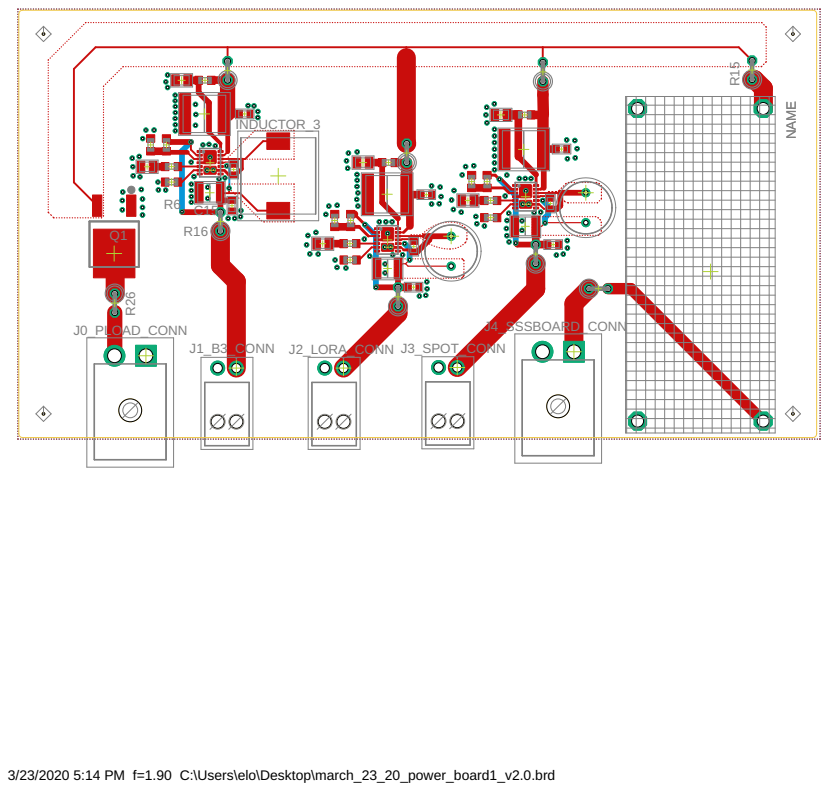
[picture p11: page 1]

3/23/2020 5:14 PM f=1.90 C:\Users\elo\Desktop\march_23_20_power_board1_v2.0.brd

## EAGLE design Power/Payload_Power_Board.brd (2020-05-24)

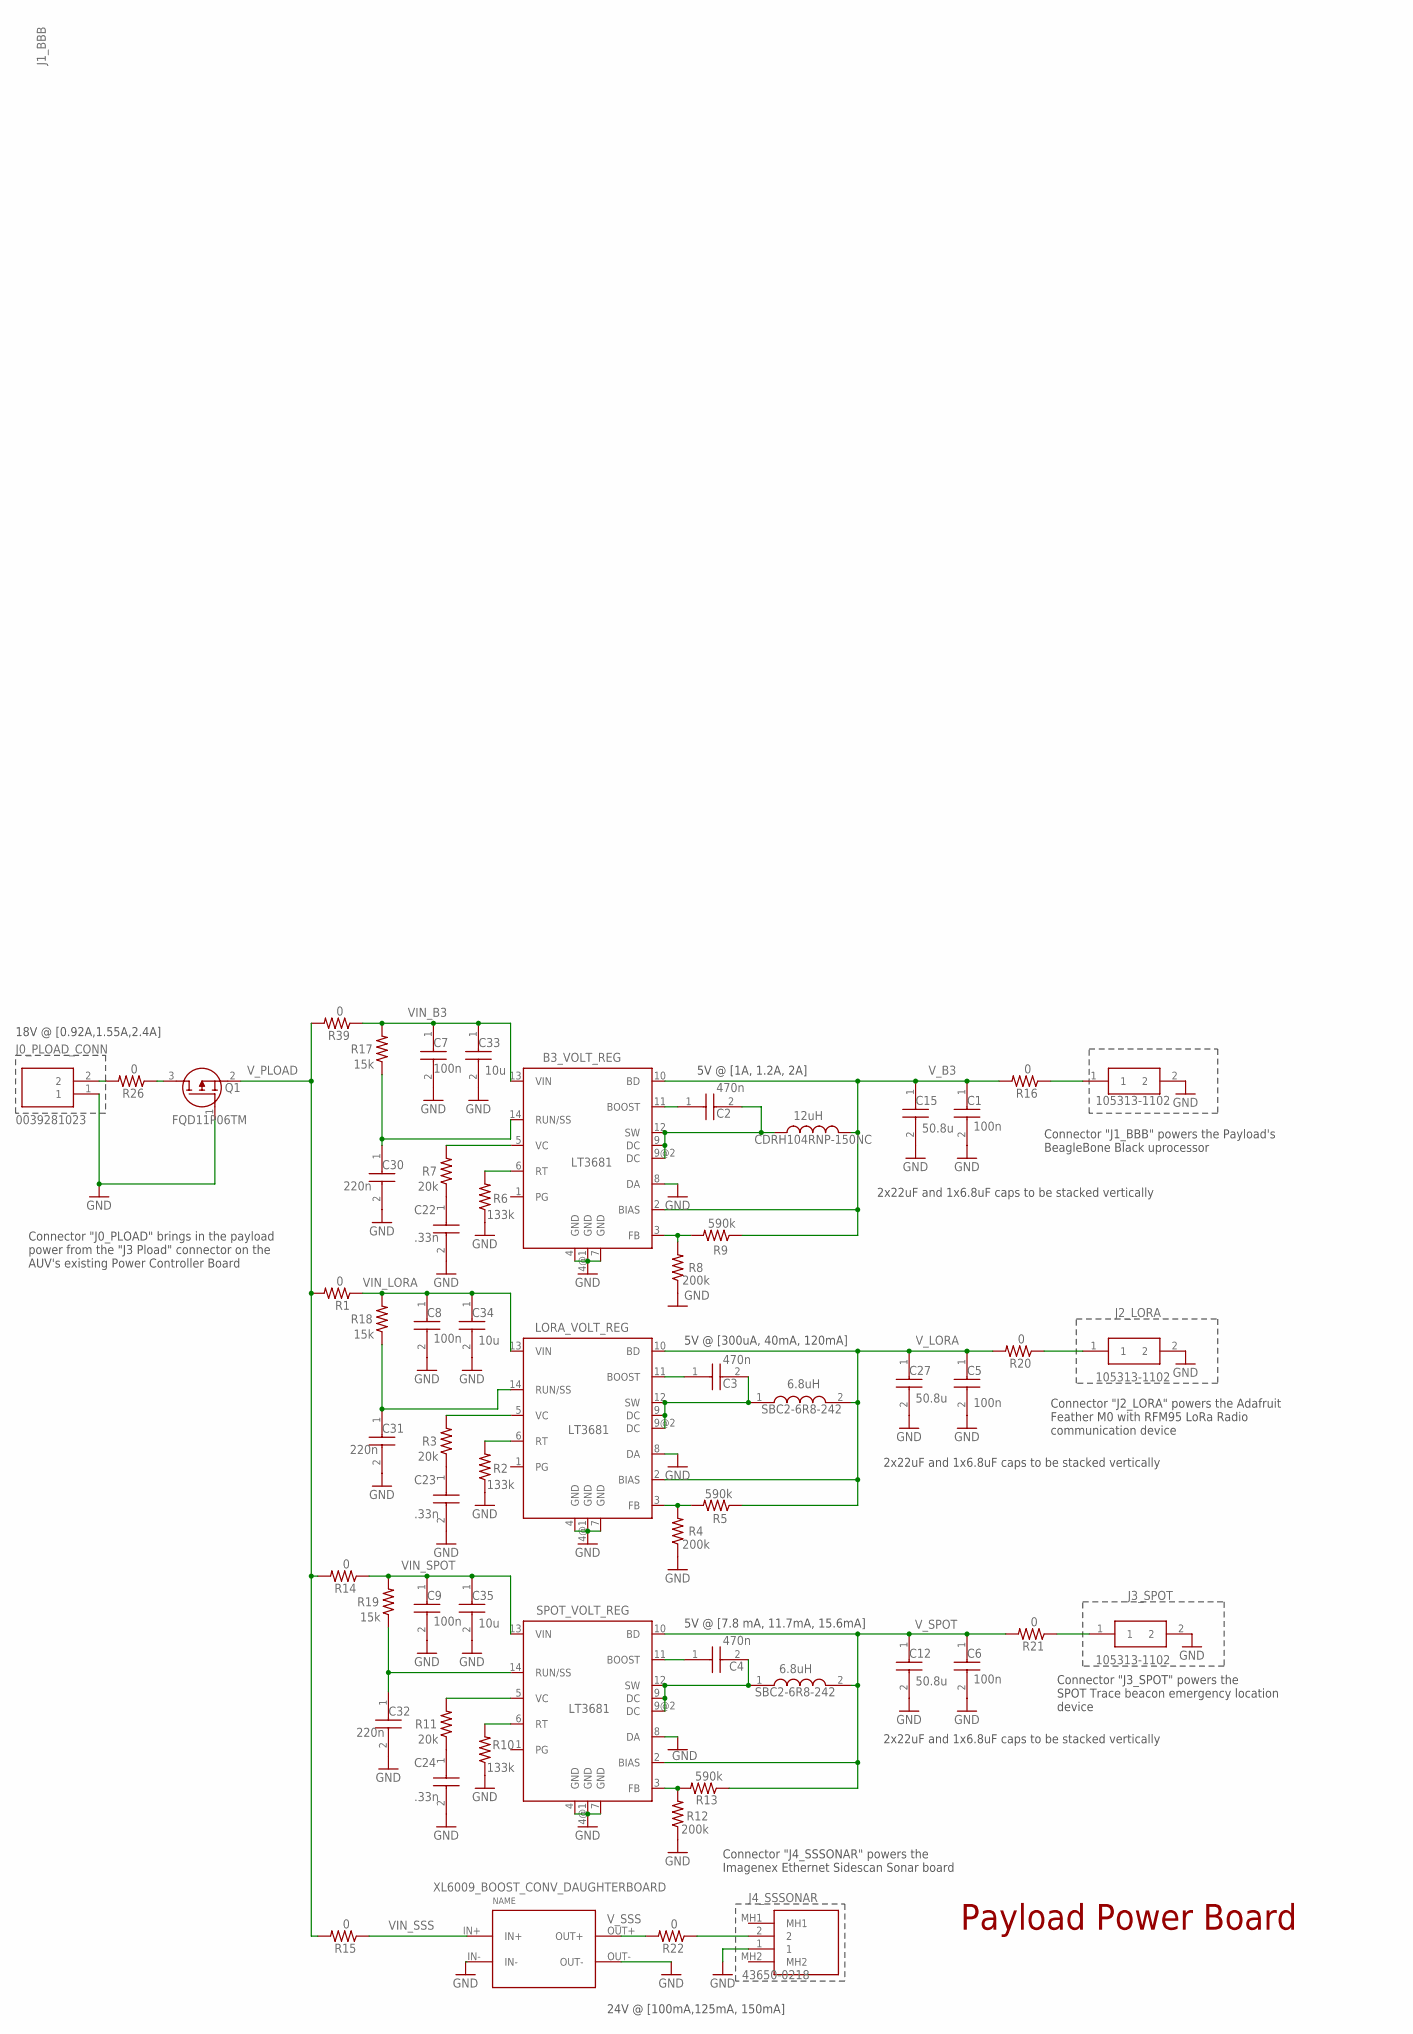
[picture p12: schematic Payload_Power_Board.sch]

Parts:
B3_VOLT_REG: LT3681; DFN14-4X3DE
C1, C5, C6, C7, C8, C9: 100n; CAPC1608X90N
C2, C3, C4: 470n; CAPC1608X90N
C12, C15, C27: 50.8u; CAPC3225X279N
C22, C23, C24: .33n; CAPC2012X140N
C30, C31, C32: 220n; CAPC2012X140N
C33, C34, C35: 10u; CAPC5750X279N
INDUCTOR_3: CDRH104RNP-150NC; INDPM102100X400N
J0_PLOAD_CONN: 0039281023; SHDR2W145P0X550_1X2_960X540X13
J1_BBB, J2_LORA, J3_SPOT: 105313-1102; 1053131102
J4_SSSONAR: 43650-0218; 436500218
L4, L5: SBC2-6R8-242; SBC26R8242
LORA_VOLT_REG: LT3681; DFN14-4X3DE
Q1: FQD11P06TM; DPAK3-CASE-369AS
R1, R14, R15, R16, R20, R21, R22, R26, R39: 0; 0207/2V; MPN RC0805FR-0710KL
R2, R6, R10: 133k; R0603
R3, R7, R11: 20k; R0603
R4, R8, R12: 200k; R0603
R5, R9, R13: 590k; R0603
R17, R18, R19: 15k; R0603
SPOT_VOLT_REG: LT3681; DFN14-4X3DE
XL6009_BOOST_CONV_DAUGHTERBOARD: XL6009; CP8-ADJ

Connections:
CBOOST_B3: B3_VOLT_REG.11 (BOOST), C2.1
CBOOST_LORA: C3.1, LORA_VOLT_REG.11 (BOOST)
CBOOST_SPOT: C4.1, SPOT_VOLT_REG.11 (BOOST)
FB_B3: B3_VOLT_REG.3 (FB), R8.2, R9.2
FB_LORA: LORA_VOLT_REG.3 (FB), R4.2, R5.2
FB_SPOT: R12.2, R13.2, SPOT_VOLT_REG.3 (FB)
GND: B3_VOLT_REG.4 (GND), B3_VOLT_REG.4@1 (GND), B3_VOLT_REG.7 (GND), B3_VOLT_REG.8 (DA), C1.2, C5.2, C6.2, C7.2, C8.2, C9.2, C12.2, C15.2, C22.2, C23.2, C24.2, C27.2, C30.2, C31.2, C32.2, C33.2, C34.2, C35.2, J0_PLOAD_CONN.1, J1_BBB.2, J2_LORA.2, J3_SPOT.2, J4_SSSONAR.1, LORA_VOLT_REG.4 (GND), LORA_VOLT_REG.4@1 (GND), LORA_VOLT_REG.7 (GND), LORA_VOLT_REG.8 (DA), Q1.1 (G), R2.1, R4.1, R6.1, R8.1, R10.1, R12.1, SPOT_VOLT_REG.4 (GND), SPOT_VOLT_REG.4@1 (GND), SPOT_VOLT_REG.7 (GND), SPOT_VOLT_REG.8 (DA), XL6009_BOOST_CONV_DAUGHTERBOARD.IN-, XL6009_BOOST_CONV_DAUGHTERBOARD.OUT-
unnamed: C22.1, R7.1
unnamed: C23.1, R3.1
unnamed: C24.1, R11.1
RT_B3: B3_VOLT_REG.6 (RT), R6.2
RT_LORA: LORA_VOLT_REG.6 (RT), R2.2
RT_SPOT: R10.2, SPOT_VOLT_REG.6 (RT)
RUN/SS_B3: B3_VOLT_REG.14 (RUN/SS), C30.1, R17.1
RUN/SS_LORA: C31.1, LORA_VOLT_REG.14 (RUN/SS), R18.1
RUN/SS_SPOT: C32.1, R19.1, SPOT_VOLT_REG.14 (RUN/SS)
SW_B3: B3_VOLT_REG.9 (DC), B3_VOLT_REG.9@2 (DC), B3_VOLT_REG.12 (SW), C2.2, INDUCTOR_3.1
SW_LORA: C3.2, L5.1, LORA_VOLT_REG.9 (DC), LORA_VOLT_REG.9@2 (DC), LORA_VOLT_REG.12 (SW)
SW_SPOT: C4.2, L4.1, SPOT_VOLT_REG.9 (DC), SPOT_VOLT_REG.9@2 (DC), SPOT_VOLT_REG.12 (SW)
VC_B3: B3_VOLT_REG.5 (VC), R7.2
VC_LORA: LORA_VOLT_REG.5 (VC), R3.2
VC_SPOT: R11.2, SPOT_VOLT_REG.5 (VC)
VIN_B3: B3_VOLT_REG.13 (VIN), C7.1, C33.1, R17.2, R39.1
VIN_LORA: C8.1, C34.1, LORA_VOLT_REG.13 (VIN), R1.1, R18.2
VIN_SPOT: C9.1, C35.1, R14.1, R19.2, SPOT_VOLT_REG.13 (VIN)
VIN_SSS: R15.1, XL6009_BOOST_CONV_DAUGHTERBOARD.IN+
V_B3: B3_VOLT_REG.2 (BIAS), B3_VOLT_REG.10 (BD), C1.1, C15.1, INDUCTOR_3.2, R9.1, R16.2
V_B31: J1_BBB.1, R16.1
V_LORA: C5.1, C27.1, L5.2, LORA_VOLT_REG.2 (BIAS), LORA_VOLT_REG.10 (BD), R5.1, R20.2
V_LORA1: J2_LORA.1, R20.1
V_PLOAD: Q1.2 (S), R1.2, R14.2, R15.2, R39.2
V_PLOAD0: Q1.3 (D), R26.1
V_PLOAD00: J0_PLOAD_CONN.2, R26.2
V_SPOT: C6.1, C12.1, L4.2, R13.1, R21.2, SPOT_VOLT_REG.2 (BIAS), SPOT_VOLT_REG.10 (BD)
V_SPOT1: J3_SPOT.1, R21.1
V_SSS: R22.2, XL6009_BOOST_CONV_DAUGHTERBOARD.OUT+
V_SSS1: J4_SSSONAR.2, R22.1

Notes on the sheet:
XL6009_BOOST_CONV_DAUGHTERBOARD
6.8uH
12uH
Payload Power Board
.33n
220n
10u
470n
50.8u
2x22uF and 1x6.8uF caps to be stacked vertically
18V @ [0.92A,1.55A,2.4A]
Connector "J1_BBB" powers the Payload's BeagleBone Black uprocessor
Connector "J2_LORA" powers the Adafruit Feather M0 with RFM95 LoRa Radio communication device
Connector "J3_SPOT" powers the SPOT Trace beacon emergency location device
Connector "J4_SSSONAR" powers the Imagenex Ethernet Sidescan Sonar board
5V @ [1A, 1.2A, 2A]
5V @ [300uA, 40mA, 120mA]
5V @ [7.8 mA, 11.7mA, 15.6mA]
24V @ [100mA,125mA, 150mA]
Connector "J0_PLOAD" brings in the payload power from the "J3 Pload" connector on the AUV's existing Power Controller Board

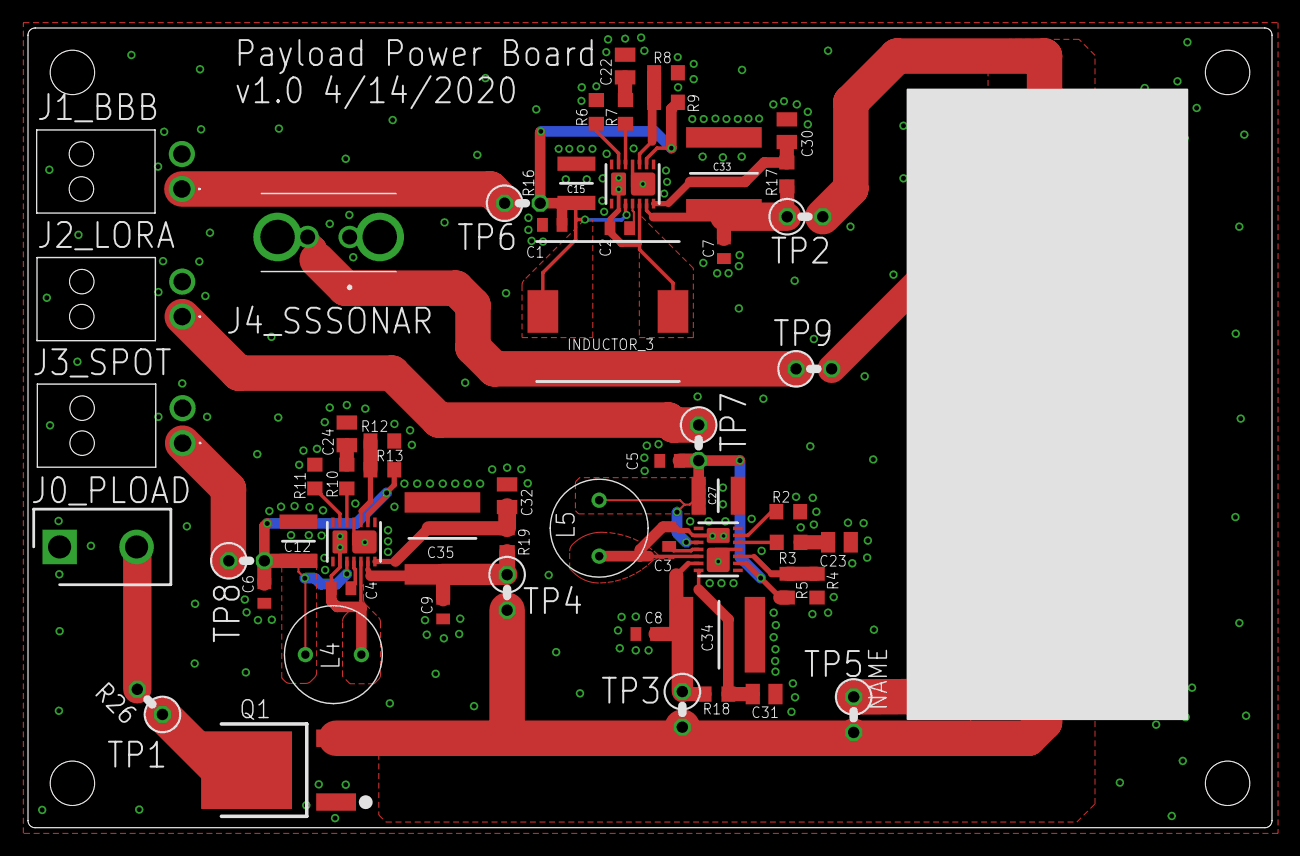
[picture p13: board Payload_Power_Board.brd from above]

Board: 2 copper layers, 88.9 x 57.1 mm, 58 parts (0 on the bottom side), 37 nets.

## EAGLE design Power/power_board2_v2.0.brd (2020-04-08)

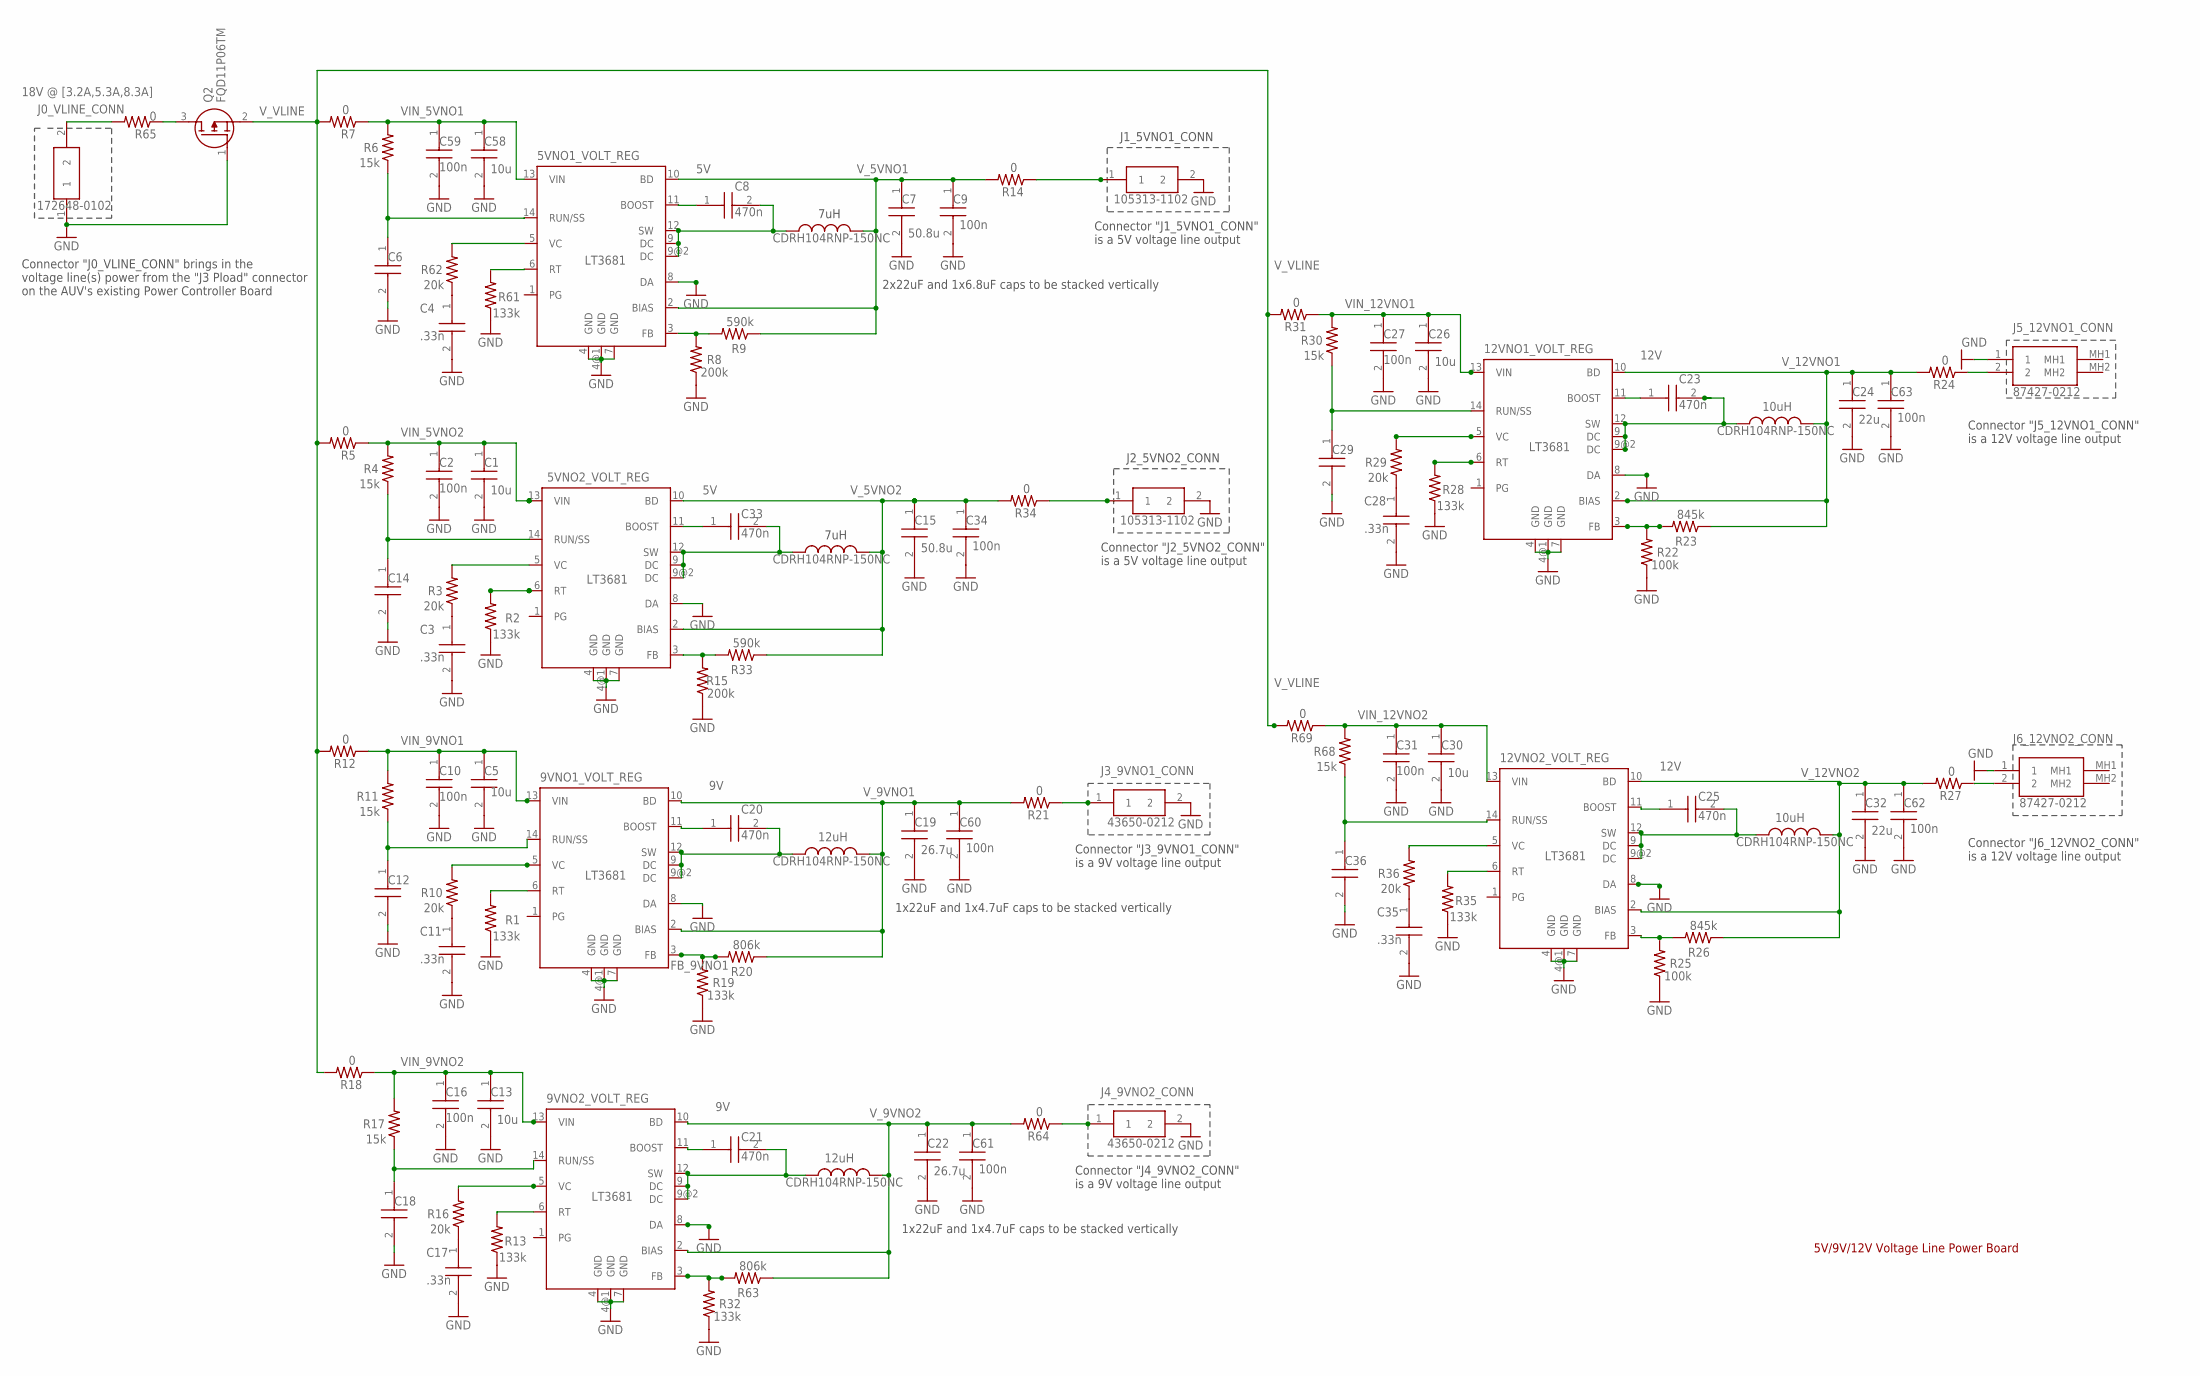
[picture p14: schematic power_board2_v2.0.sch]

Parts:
5VNO1_VOLT_REG, 5VNO2_VOLT_REG, 9VNO1_VOLT_REG, 9VNO2_VOLT_REG, 12VNO1_VOLT_REG, 12VNO2_VOLT_REG: LT3681; DFN14-4X3DE
C1, C5, C13, C26, C30, C58: 10u; CAPC5750X279N
C2, C9, C10, C16, C27, C31, C34, C59, C60, C61, C62, C63: 100n; CAPC1608X90N
C3, C4, C11, C17, C28, C35: .33n; CAPC2012X140N
C6, C12, C14, C18, C29, C36: 220n; CAPC2012X140N
C7, C15: 50.8u; CAPC3225X279N
C8, C20, C21, C23, C25, C33: 470n; CAPC1608X90N
C19, C22: 26.7u; CAPC3225X279N
C24, C32: 22u; CAPC3225X279N
INDUCTOR_2, INDUCTOR_4, INDUCTOR_5, INDUCTOR_6, INDUCTOR_7, INDUCTOR_8: CDRH104RNP-150NC; INDPM102100X400N
J0_VLINE_CONN: 172648-0102; 1726480102
J1_5VNO1_CONN, J2_5VNO2_CONN: 105313-1102; 1053131102
J3_9VNO1_CONN, J4_9VNO2_CONN: 43650-0212; 43650-0214
J5_12VNO1_CONN, J6_12VNO2_CONN: 87427-0212; 874270212
Q2: FQD11P06TM; DPAK3-CASE-369AS
R1, R2, R13, R19, R28, R32, R35, R61: 133k; R0603
R3, R10, R16, R29, R36, R62: 20k; R0603
R4, R6, R11, R17, R30, R68: 15k; R0603
R5, R7, R12, R14, R18, R21, R24, R27, R31, R34, R64, R65, R69: 0; 0207/2V; MPN RC0805FR-0710KL
R8, R15: 200k; R0603
R9, R33: 590k; R0603
R20, R63: 806k; R0603
R22, R25: 100k; R0603
R23, R26: 845k; R0603

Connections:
CBOOST_5VNO1: 5VNO1_VOLT_REG.11 (BOOST), C8.1
CBOOST_5VNO2: 5VNO2_VOLT_REG.11 (BOOST), C33.1
CBOOST_9VNO1: 9VNO1_VOLT_REG.11 (BOOST), C20.1
CBOOST_9VNO2: 9VNO2_VOLT_REG.11 (BOOST), C21.1
CBOOST_12VNO1: 12VNO1_VOLT_REG.11 (BOOST), C23.1
CBOOST_12VNO2: 12VNO2_VOLT_REG.11 (BOOST), C25.1
FB_5VNO1: 5VNO1_VOLT_REG.3 (FB), R8.2, R9.2
FB_5VNO2: 5VNO2_VOLT_REG.3 (FB), R15.2, R33.2
FB_9VNO1: 9VNO1_VOLT_REG.3 (FB), R19.2, R20.2
FB_9VNO2: 9VNO2_VOLT_REG.3 (FB), R32.2, R63.2
FB_12VNO1: 12VNO1_VOLT_REG.3 (FB), R22.2, R23.2
FB_12VNO2: 12VNO2_VOLT_REG.3 (FB), R25.2, R26.2
GND: 5VNO1_VOLT_REG.4 (GND), 5VNO1_VOLT_REG.4@1 (GND), 5VNO1_VOLT_REG.7 (GND), 5VNO1_VOLT_REG.8 (DA), 5VNO2_VOLT_REG.4 (GND), 5VNO2_VOLT_REG.4@1 (GND), 5VNO2_VOLT_REG.7 (GND), 5VNO2_VOLT_REG.8 (DA), 9VNO1_VOLT_REG.4 (GND), 9VNO1_VOLT_REG.4@1 (GND), 9VNO1_VOLT_REG.7 (GND), 9VNO1_VOLT_REG.8 (DA), 9VNO2_VOLT_REG.4 (GND), 9VNO2_VOLT_REG.4@1 (GND), 9VNO2_VOLT_REG.7 (GND), 9VNO2_VOLT_REG.8 (DA), 12VNO1_VOLT_REG.4 (GND), 12VNO1_VOLT_REG.4@1 (GND), 12VNO1_VOLT_REG.7 (GND), 12VNO1_VOLT_REG.8 (DA), 12VNO2_VOLT_REG.4 (GND), 12VNO2_VOLT_REG.4@1 (GND), 12VNO2_VOLT_REG.7 (GND), C1.2, C2.2, C3.2, C4.2, C5.2, C6.2, C7.2, C9.2, C10.2, C11.2, C12.2, C13.2, C14.2, C15.2, C16.2, C17.2, C18.2, C19.2, C22.2, C24.2, C26.2, C27.2, C28.2, C29.2, C30.2, C31.2, C32.2, C34.2, C35.2, C36.2, C58.2, C59.2, C60.2, C61.2, C62.2, C63.2, J0_VLINE_CONN.1, J1_5VNO1_CONN.2, J2_5VNO2_CONN.2, J3_9VNO1_CONN.2, J4_9VNO2_CONN.2, J5_12VNO1_CONN.1, J6_12VNO2_CONN.1, Q2.1 (G), R1.1, R2.1, R8.1, R13.1, R15.1, R19.1, R22.1, R25.1, R28.1, R32.1, R35.1, R61.1
unnamed: C4.1, R62.1
unnamed: C3.1, R3.1
unnamed: C11.1, R10.1
unnamed: C17.1, R16.1
unnamed: C28.1, R29.1
unnamed: C35.1, R36.1
RT_5VNO1: 5VNO1_VOLT_REG.6 (RT), R61.2
RT_5VNO2: 5VNO2_VOLT_REG.6 (RT), R2.2
RT_9VNO1: 9VNO1_VOLT_REG.6 (RT), R1.2
RT_9VNO2: 9VNO2_VOLT_REG.6 (RT), R13.2
RT_12VNO1: 12VNO1_VOLT_REG.6 (RT), R28.2
RT_12VNO2: 12VNO2_VOLT_REG.6 (RT), R35.2
RUN/SS_5VNO1: 5VNO1_VOLT_REG.14 (RUN/SS), C6.1, R6.1
RUN/SS_5VNO2: 5VNO2_VOLT_REG.14 (RUN/SS), C14.1, R4.1
RUN/SS_9VNO1: 9VNO1_VOLT_REG.14 (RUN/SS), C12.1, R11.1
RUN/SS_9VNO2: 9VNO2_VOLT_REG.14 (RUN/SS), C18.1, R17.1
RUN/SS_12VNO1: 12VNO1_VOLT_REG.14 (RUN/SS), C29.1, R30.1
RUN/SS_12VNO2: 12VNO2_VOLT_REG.14 (RUN/SS), C36.1, R68.1
SW_5VNO1: 5VNO1_VOLT_REG.9 (DC), 5VNO1_VOLT_REG.9@2 (DC), 5VNO1_VOLT_REG.12 (SW), C8.2, INDUCTOR_2.1
SW_5VNO2: 5VNO2_VOLT_REG.9 (DC), 5VNO2_VOLT_REG.9@2 (DC), 5VNO2_VOLT_REG.12 (SW), C33.2, INDUCTOR_4.1
SW_9VNO1: 9VNO1_VOLT_REG.9 (DC), 9VNO1_VOLT_REG.9@2 (DC), 9VNO1_VOLT_REG.12 (SW), C20.2, INDUCTOR_5.1
SW_9VNO2: 9VNO2_VOLT_REG.9 (DC), 9VNO2_VOLT_REG.9@2 (DC), 9VNO2_VOLT_REG.12 (SW), C21.2, INDUCTOR_6.1
SW_12VNO1: 12VNO1_VOLT_REG.9 (DC), 12VNO1_VOLT_REG.9@2 (DC), 12VNO1_VOLT_REG.12 (SW), C23.2, INDUCTOR_7.1
SW_12VNO2: 12VNO2_VOLT_REG.9 (DC), 12VNO2_VOLT_REG.9@2 (DC), 12VNO2_VOLT_REG.12 (SW), C25.2, INDUCTOR_8.1
VC_5VNO1: 5VNO1_VOLT_REG.5 (VC), R62.2
VC_5VNO2: 5VNO2_VOLT_REG.5 (VC), R3.2
VC_9VNO1: 9VNO1_VOLT_REG.5 (VC), R10.2
VC_9VNO2: 9VNO2_VOLT_REG.5 (VC), R16.2
VC_12VNO1: 12VNO1_VOLT_REG.5 (VC), R29.2
VC_12VNO2: 12VNO2_VOLT_REG.5 (VC), R36.2
VIN_5VNO1: 5VNO1_VOLT_REG.13 (VIN), C58.1, C59.1, R6.2, R7.1
VIN_5VNO2: 5VNO2_VOLT_REG.13 (VIN), C1.1, C2.1, R4.2, R5.1
VIN_9VNO1: 9VNO1_VOLT_REG.13 (VIN), C5.1, C10.1, R11.2, R12.1
VIN_9VNO2: 9VNO2_VOLT_REG.13 (VIN), C13.1, C16.1, R17.2, R18.1
VIN_12VNO1: 12VNO1_VOLT_REG.13 (VIN), C26.1, C27.1, R30.2, R31.1
VIN_12VNO2: 12VNO2_VOLT_REG.13 (VIN), C30.1, C31.1, R68.2, R69.1
V_5VNO1: 5VNO1_VOLT_REG.2 (BIAS), 5VNO1_VOLT_REG.10 (BD), C7.1, C9.1, INDUCTOR_2.2, R9.1, R14.2
V_5VNO1_0: J1_5VNO1_CONN.1, R14.1
V_5VNO2: 5VNO2_VOLT_REG.2 (BIAS), 5VNO2_VOLT_REG.10 (BD), C15.1, C34.1, INDUCTOR_4.2, R33.1, R34.2
V_5VNO2_0: J2_5VNO2_CONN.1, R34.1
V_9VNO1: 9VNO1_VOLT_REG.2 (BIAS), 9VNO1_VOLT_REG.10 (BD), C19.1, C60.1, INDUCTOR_5.2, R20.1, R21.2
V_9VNO1_0: J3_9VNO1_CONN.1, R21.1
V_9VNO2: 9VNO2_VOLT_REG.2 (BIAS), 9VNO2_VOLT_REG.10 (BD), C22.1, C61.1, INDUCTOR_6.2, R63.1, R64.2
V_9VNO2_0: J4_9VNO2_CONN.1, R64.1
V_12VNO1: 12VNO1_VOLT_REG.2 (BIAS), 12VNO1_VOLT_REG.10 (BD), C24.1, C63.1, INDUCTOR_7.2, R23.1, R24.2
V_12VNO1_0: J5_12VNO1_CONN.2, R24.1
V_12VNO2: 12VNO2_VOLT_REG.2 (BIAS), 12VNO2_VOLT_REG.10 (BD), C32.1, C62.1, INDUCTOR_8.2, R26.1, R27.2
V_12VNO2_0: J6_12VNO2_CONN.2, R27.1
V_VLINE: Q2.2 (S), R5.2, R7.2, R12.2, R18.2, R31.2, R69.2
V_VLINE00: J0_VLINE_CONN.2, R65.2
V_VLINE0: Q2.3 (D), R65.1

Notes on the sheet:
10u
.33n
50.8u
2x22uF and 1x6.8uF caps to be stacked vertically
J1_5VNO1_CONN
7uH
J2_5VNO2_CONN
12uH
Connector "J2_5VNO2_CONN" is a 5V voltage line output
Connector "J1_5VNO1_CONN" is a 5V voltage line output
18V @ [3.2A,5.3A,8.3A]
Connector "J0_VLINE_CONN" brings in the voltage line(s) power from the "J3 Pload" connector on the AUV's existing Power Controller Board
26.7u
22u
1x22uF and 1x4.7uF caps to be stacked vertically
Connector "J3_9VNO1_CONN" is a 9V voltage line output
5V/9V/12V Voltage Line Power Board
10uH
Connector "J4_9VNO2_CONN" is a 9V voltage line output
12V
Connector "J5_12VNO1_CONN" is a 12V voltage line output
Connector "J6_12VNO2_CONN" is a 12V voltage line output

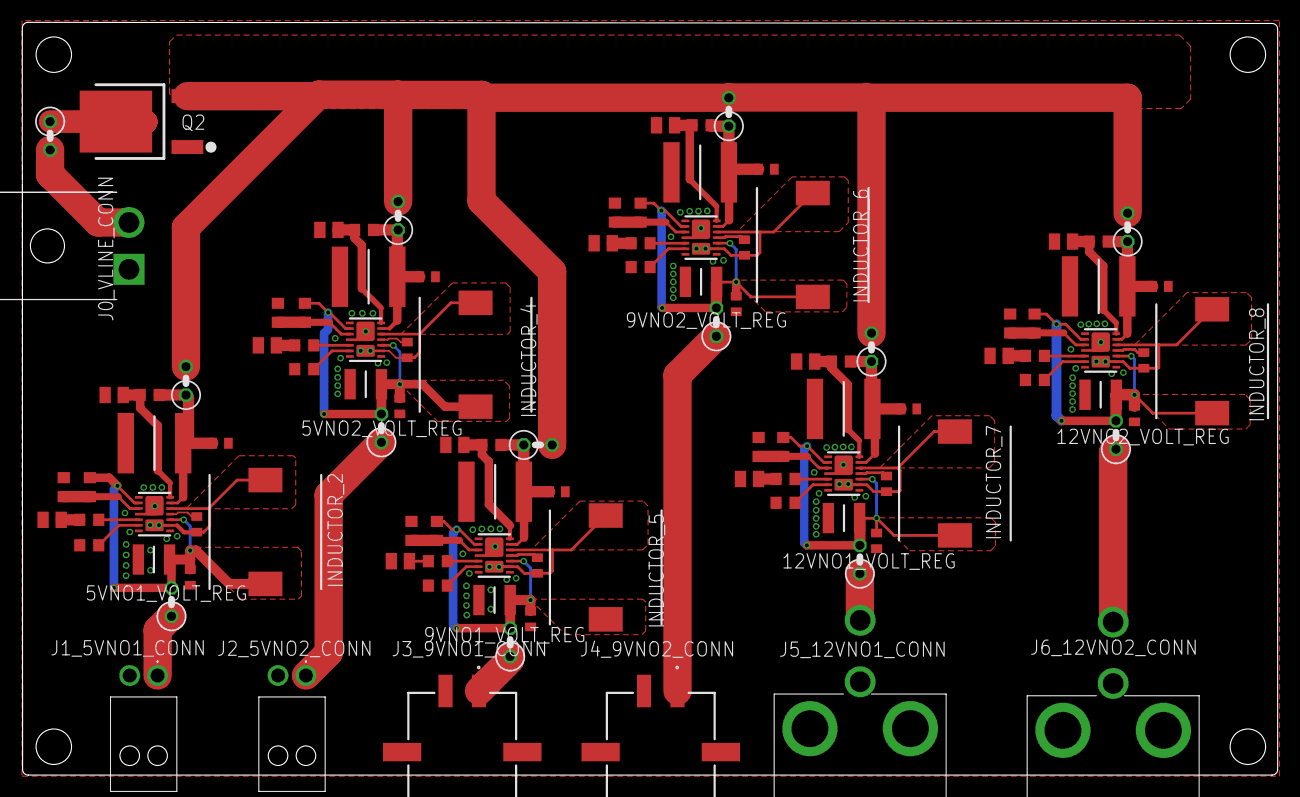
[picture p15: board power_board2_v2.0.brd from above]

Board: 2 copper layers, 112.4 x 67.4 mm, 105 parts (0 on the bottom side), 64 nets.

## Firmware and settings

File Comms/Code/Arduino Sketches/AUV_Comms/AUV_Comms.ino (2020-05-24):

// AUV LoRa Link Arduino Sketch
// This revision: v.1.0;
// Original authorship: Jeff Roman, 04/2020
// PSU Capstone Team: Wracksweeper/WAVES

// Designed for use with Adafruit Feather M0 packaged with onboard HopeRF RFM95 LoRa module.
// Battery monitoring provided by setting a voltage divider of 2 2.2k resistors from the
// "USB" pin to analog pin A2 to ground.

// CURRENT FUNCTIONALITY:
// This is the Shore Client-enabled sketch of the terminal-over-LoRa software which enables
// a team to remotely query and direct the MOOS community running in a surfaced AUV within
// range of the RF link. It transmits any serial input up to 100 bytes (more possible based
// on specific link settings) to a shore client, and conveys any received data as UART
// output when set as an AUV/server. It also reports a help signal every 30 seconds if it loses
// USB power, and reports when its backup battery is below 30% (imminent loss). When set as
// shore client, it provides wireless transmission of all serial input up to 100 bytes and
// returns any response. In shore client mode, there is a feature LINKMON which also includes
// data on RF link quality (RSSI, SNR) which is turned on by the method "-verb" (verbose output).

// There is a method -changemode which can be invoked from either side that can allow
// a switch to different RF link settings for faster datarate in better link environments or
// slower transfer in areas with poor link quality.  If the shore client is disconnected while
// AUV is at sea, can change settings to match the AUV without required handshake by using the
// call "-changeme" instead with the same syntax. All messaging is ACK-based and CRC'ed,
// with CRC coding settable with -changemode. For SNR/RSSI information, packet time, and Hex
// translations of packets sent or received invoke "-verb" at the command line.

// The AUV server mode is intended to interface with a custom UART daemon which properly
// deals with any of the valid inputs.

// The shore client mode is intended to interface with a CLI-based python script which will
// display received messages and allow the user to choose to send any output along to a local
// MOOS community.

// DESIRED FUTURE FUNCTIONALITY:
// 1) A getGPS procedure for inclusion and regular transmission from AUV while it's floating.
//    This will require a query to BBB, with the last known GPS sentence stored in case BBB
//    dies for inclusion in help message transmissions.
// 2) A "help" dialogue which can be entered from the shore client command line to access
//    available calls and get guidance.
// 3) A more extensible flag system for non-terminal methods like -changemode that only affect
//    the arduinos.
// 4) A buffer handler to enable data of arbitrary size to be transmitted with full reliable
//    datagram accuracy, enabling "upload" and "download" capabilities.
// 5) Smarter battery check function to estimate remaining lifespan based on timer and some
//    conservative average total power consumption figure. I estimate 100mA based on ~170-200mA
//    for duration of transmit and ~40mA quiescent listening current (we can query the arduino
//    itself for information about the saved AUV states like GPS, internal moisture information
//    if available, etc. Below 30% battery, should also flag a low-power state that puts radio
//    to sleep between help messages.

// For use or test as Shore Client radio: leave DEBUG defined, leave SHORE_CLIENT defined

// For use as AUV radio over UART: comment out #define DEBUG and #define SHORE_CLIENT

// For test over USB as AUV radio: comment out #define SHORE_CLIENT but leave DEBUG uncommented

#include <SPI.h>
#include <RH_RF95.h> // this and RHReliableDatagram from https://github.com/adafruit/RadioHead
#include <avr/dtostrf.h>
#include <RHReliableDatagram.h>
#include <string.h>
#include <MemoryFree.h>  // get from https://github.com/mpflaga/Arduino-MemoryFree 

//------------------------------STATE DEFINITIONS-----------------------------------------

//---------WARNING-----------WARNING-------------WARNING-------------WARNING--------------
//------------------------THIS SKETCH IS THE SERVER(ADDRESS 1)----------------------------
//-------------IT IS IMPORTANT NOT TO USE THE SAME SKETCH FOR BOTH RADIOS-----------------
//-------------------THIS IS INTENDED TO BE ONBOARD THE AUV-------------------------------


#define SHORE_CLIENT            /* UNCOMMENT FOR SHORE CLIENT, COMMENT FOR AUV SERVER */
#ifdef SHORE_CLIENT
const bool SHORE = true;
#define MY_ADDRESS 66
#define REMOTE_ADDRESS 69
#else
const bool SHORE = false;
#define MY_ADDRESS 69
#define REMOTE_ADDRESS 66
#endif

//============WARNING====================WARNING===============WARNING==================
// COMMENT OUT THE DEFINITION OF DEBUG FOR USE INSIDE AUV. DEBUG MODE DIRECTS ALL SERIAL
// DATA TO USB INSTEAD OF UART! CANNOT TEST RADIO OVER USB SERIAL IF NOT IN DEBUG MODE!!

#define DEBUG             /* comment this line when uploading to AUV radio*/
#ifdef DEBUG
bool db = true;
auto hsp = Serial; // use USB serial in debug
#define debug_print(x) hsp.println(x); // provide method for tracing errors
#define debug_hold() while(!hsp){delay(1);};
#else
bool db = false;

#define hsp Serial1  // normal operation use UART
#define debug_print(x)
#define debug_hold()
#endif

//-------------------------PIN DEFINITIONS------------------------------------------------

// For battery check, USB power check.
#define VBATPIN A7 // pin D9 on feather board
#define USB_PRESENT A2
#define USB_VOLTAGE 2.2   // half of maximum battery voltage. if USB pwr is gone
// the USB pin will read vBatt instead of 4.6-5.5.
#define LED 13

// for feather m0
#define RFM95_CS 8
#define RFM95_RST 4
#define RFM95_INT 3

//--------------------------LORA SETTINGS DEFS---------------------------------------------

// Change to 434.0 or other frequency, must match RX's freq!
#define RF95_FREQ 915.0
#define TIMEOUT 4000
#define RETRIES 3

// EFFECTS OF CHANGING BW: -3dB link budget for each doubling of BW
// but datarate can effectively double.
// EFFECTS of CHANGING SF: +2.5dB link budget for each increase of SF
// but datarate cuts in half.
// EFFECTS OF CHANGING CR: Datarate penalty relative to how many chars
// are used just for CRC vs. how many used for payload.

// Fastest Packet time - bw500cr45 sf128, ~0.1s
// Slowest Packet time - bw125cr48 sf4096, ~7s

// Pending distance testing, recommend default bw125cr47 sf1024 for best
// balance of link budget, reliability, and datarate. ~2s packet time.

// SETTING OPTIONS FOR REGISTER 1D

const byte bw125cr45 = 0x72;
const byte bw125cr46 = 0x74;
const byte bw125cr47 = 0x76;
const byte bw125cr48 = 0x78;
const byte bw250cr45 = 0x82;
const byte bw250cr46 = 0x84;
const byte bw250cr47 = 0x86;
const byte bw250cr48 = 0x88;
const byte bw500cr45 = 0x92;
const byte bw500cr46 = 0x94;
const byte bw500cr47 = 0x96;
const byte bw500cr48 = 0x98;


// SETTING OPTIONS FOR REGISTER 1E

const byte sf128 = 0x74;
const byte sf256 = 0x84;
const byte sf512 = 0x94;
const byte sf1024 = 0xA4;
const byte sf2048 = 0xB4;
const byte sf4096 = 0xC4;

typedef struct {
  char *key;
  byte val;
} t_symstruct;   // create struct for setting LUTs

static t_symstruct bwLUT[] = {
  {"bw125cr45\0", bw125cr45}, {"bw250cr45\0", bw250cr45}, {"bw500cr45\0", bw500cr45},
  {"bw125cr46\0", bw125cr46}, {"bw250cr46\0", bw250cr46}, {"bw500cr46\0", bw500cr46},
  {"bw125cr47\0", bw125cr47}, {"bw250cr47\0", bw250cr47}, {"bw500cr47\0", bw500cr47},
  {"bw125cr48\0", bw125cr48}, {"bw250cr48\0", bw250cr48}, {"bw500cr48\0", bw500cr48}
};

static t_symstruct sfLUT[] = {
  {"sf128\0", sf128}, {"sf256\0", sf256}, {"sf512\0", sf512},
  {"sf1024\0", sf1024}, {"sf2048\0", sf2048}, {"sf4096\0", sf4096}
};

#define N_bwKeys 12
#define N_sfKeys 6

// Singleton instance of the radio driver
RH_RF95 driver(RFM95_CS, RFM95_INT);                // driver is radio hardware driver
RHReliableDatagram rf95(driver, MY_ADDRESS);    // rf95 is the msg manager

//----------------------------GLOBAL VARIABLES-----------------------------------------------

// set vars for serial input function
const byte numChars = 255;  // limits read to 255 bytes (full size of serial buffer
// and max length of a lora payload)
const int totalMem = 262144;
byte msgBuffer[numChars];   // Serial input buffer
char locationString[numChars];   // store last known GPS data
bool newData = false;
byte set[3];      // global array to hold the settings
byte buf[numChars];      // receive buffer
byte len = sizeof(buf);
byte from;
// command keywords
const char MODE[] = "-changemode\0";
const char MODESOLO[] = "-changeme\0";
const char RCVD[] = "-received-\0";
const char VERBOSITY[] = "-verb\0";
const char MEMOSITY[] = "-memmon\0";
int memDiff;
int lastMem = freeMemory();
float memPct;
int timer = millis();
bool OUTMON = false;          // monitor RF link quality
bool MEMMON = false;          // monitor memorymemory

//------------------------------GLOBAL FUNCTIONS---------------------------------------------

// Blinky blinky. Insert ledFlash(n) in suspect spots if trying to troubleshoot hardware
// when using over UART (no usb serial). Each flash takes 200ms. THIS IS A BLOCKING FUNCTION.
void ledFlash(int n) {
  int i = 0;
  while (i < n) {
    digitalWrite(LED, HIGH);
    delay(100);
    digitalWrite(LED, LOW);
    delay(100);
    i++;
  }
}

//~~~~~~~~~~~~~~~~~~~~~~~~~~~~~~~~~~~~~~~~~~~~~~~~~~~~~~~~~~~~~~~~~~~~~~~~~~~~~~~~~~~~~~~~~~~
//
//---------------------------------SETUP-----------------------------------------------------
//
//~~~~~~~~~~~~~~~~~~~~~~~~~~~~~~~~~~~~~~~~~~~~~~~~~~~~~~~~~~~~~~~~~~~~~~~~~~~~~~~~~~~~~~~~~~~

void setup()
{
  pinMode(RFM95_RST, OUTPUT);
  digitalWrite(RFM95_RST, HIGH);
  pinMode(LED, OUTPUT);
  digitalWrite(LED, LOW);
  ledFlash(2);
  digitalWrite(LED, HIGH);
  hsp.begin(9600);
  digitalWrite(LED, LOW);
  debug_hold();
  delay(100);
  if (SHORE) {
    hsp.println("Welcome to the AUV Remote Command Center.");
    hsp.println("Please limit packets to 100 characters. Type and press enter to send.");
  }
  else {
    debug_print("I am an AUV. This is how I talk!");
    ledFlash(10);
  }

  // manual reset
  digitalWrite(RFM95_RST, LOW);
  delay(10);
  digitalWrite(RFM95_RST, HIGH);
  delay(10);

  //-------------------------RFM95 Configuration Time------------------

  while (!rf95.init()) {
    debug_print("LoRa radio init failed");
    debug_print("Uncomment '#define SERIAL_DEBUG' in RH_RF95.cpp for detailed debug info");
    while (1) {
      ledFlash(1);
    }
  }
  debug_print("LoRa radio init OK!");

  // Defaults after init are 434.0MHz, modulation GFSK_Rb250Fd250, +13dbM
  if (!driver.setFrequency(RF95_FREQ)) {
    debug_print("setFrequency failed");
    while (1) {
      ledFlash(1);
    }
  }
  debug_print("Set Freq to: "); debug_print(RF95_FREQ);

  // Initial transmission settings
  // DEFAULT: FASTEST DATARATE AVAILABLE

  RH_RF95::ModemConfig modem_config = {
    bw500cr45,
    sf256,
    0x0C  // LEAVE THIS ALONE
  };

  driver.setModemRegisters(&modem_config);
  //set to maximum possible output power
  driver.setTxPower(23, false);
  rf95.setRetries(RETRIES);
  rf95.setTimeout(TIMEOUT);
}

//------------------Serial Input Methods----------------------------------------------------

// This method only safe with up to 255 chars


void receiveLine() {
  static byte ndx = 0;
  byte endMarker = '\n';
  byte backSpace = '\b';
  byte rc;
  while (hsp.available() > 0) {
    rc = hsp.read();
    if ((rc != endMarker) && (rc != backSpace) && (ndx < (numChars - 1))) {
      msgBuffer[ndx] = rc;
      ndx++;
      if (ndx >= numChars) {
        ndx = numChars - 1;
      }
    }
    else if (rc == backSpace) {
      ndx--;
      if (ndx < 0) {
        ndx = 0;
      }
      msgBuffer[ndx] = 0;
    }
    else {
      msgBuffer[ndx] = '\0';
      ndx++;
      msgBuffer[ndx] = endMarker;
      ndx = 0;
      newData = true;
    }
  }
}

//------------------Look Up Table Access for Settings -----------------------------------

int keyfromstring(char *key, int param)  // param = 0 for bw/cr, 1 for sf
{
  int NKEYS;
  if (param == 2) {
    NKEYS = N_sfKeys;
    for (int i = 0; i < NKEYS; i++) {
      if (strcmp(sfLUT[i].key, key) == 0) {
        debug_print("matched.")
        debug_print(key);
        return sfLUT[i].val;
      }
    }
  }
  else {
    NKEYS = N_bwKeys;
    for (int i = 0; i < NKEYS; i++) {
      if (strcmp(bwLUT[i].key, key) == 0) {
        debug_print("matched.")
        debug_print(key);
        return bwLUT[i].val;
      }
    }
  }
  return -1;
}

//------------------------------LoRa methods---------------------------------------------

void transmit(byte msg[], int msgLength) {
  int packetTime = millis();
  if (!rf95.sendtoWait((uint8_t *)msg, msgLength + 1, REMOTE_ADDRESS)) {
    debug_print("Transmission failed. No ACK received.");
  }

  else {
    if (SHORE) {
      hsp.println("Transmission successful.");
      if (OUTMON) {
        hsp.println("Bytes sent: ");
        for (int i = 0; i <= msgLength; i++) {
          hsp.print(msg[i], HEX);
        }
        hsp.print("\n");
        packetTime = millis() - packetTime;
        hsp.print(packetTime / 1000.0); hsp.println(" seconds packet time.");
      }
    }
  }
}

//-------------------------Initiate Settings Change Handshake-----------------------------

int modeChangeLocal(byte msg[], bool BOTH) {
  set[2] = 0;
  int c = 0;
  char msgCopy[numChars];
  strcpy(msgCopy, (char*)msg);
  char* rest = msgCopy;
  char* token = strtok(rest, "\n");       // clean off newline
  token = strtok(rest, "\r");       // clean off carriage return

  while (token = strtok_r(rest, " ", &rest)) {
    if (c == 1) {
      switch (keyfromstring(token, c)) {  // param 0 corresponds to bw,cr parameter
        case -1:
          hsp.println("not a valid setting.");
          hsp.println("Try again with the settings format - changemode bw___cr__ sf___");
          set[2] = 1;    // must check set[2] to ensure valid overall settings
          break;
        case bw125cr45: set[0] = bw125cr45; break;
        case bw125cr46: set[0] = bw125cr46; break;
        case bw125cr47: set[0] = bw125cr47; break;
        case bw125cr48: set[0] = bw125cr48; break;
        case bw250cr45: set[0] = bw250cr45; break;
        case bw250cr46: set[0] = bw250cr46; break;
        case bw250cr47: set[0] = bw250cr47; break;
        case bw250cr48: set[0] = bw250cr48; break;
        case bw500cr45: set[0] = bw500cr45; break;
        case bw500cr46: set[0] = bw500cr46; break;
        case bw500cr47: set[0] = bw500cr47; break;
        case bw500cr48: set[0] = bw500cr48; break;
      }
    }

    if (c == 2) {
      switch (keyfromstring(token, c)) {
        case -1:
          hsp.println("not a valid setting.");
          hsp.println("Try again with the settings format - changemode bw___cr__ sf___");
          set[2] = 1;    // must check set[2] to ensure valid overall settings
          break;
        case sf128: set[1] = sf128; break;
        case sf256: set[1] = sf256; break;
        case sf512: set[1] = sf512; break;
        case sf1024: set[1] = sf1024; break;
        case sf2048: set[1] = sf2048; break;
        case sf4096: set[1] = sf4096; break;
      }
    }
    c++;
  }

  if (set[2] == 1) {
    return -1;
  }
  if (BOTH) {
    if (!rf95.sendtoWait(msg, strlen((char*)msg) + 1, REMOTE_ADDRESS)) {
      hsp.println("Couldn't send the new settings, cannot change mode.");
      return -1;
    }
  }
  if (!BOTH) {
    debug_print("Changing mode now.");
    RH_RF95::ModemConfig new_modem_config = {
      set[0],
      set[1],
      0x0C  // LEAVE THIS ALONE
    };
    delay(100);
    driver.setModemRegisters(&new_modem_config);      // give it the configuration we specified
    delay(100);
  }

  else {
    return 0;
  }
}

//-----------------------Reciprocate Settings Change Handshake-------------------------

int modeChangeRemote(byte msg[]) {

  set[2] = 0;
  int sC = 0;
  debug_print("The char array looks like: ");
  debug_print((char*)msg);
  char msgCopy[numChars];
  char newBWCR[] = "";
  char newSF[] = "";
  strcpy(msgCopy, (char*)msg);
  char* rest = msgCopy;         // pointer for tokenizing
  char* token = strtok(rest, " ");
  while (token != NULL) {
    switch (keyfromstring(token, 1)) {  // param corresponds to bw,cr parameter
      case -1: break;
      case bw125cr45: set[0] = bw125cr45; strcat(newBWCR, "125kHz, 4_5, "); sC++; break;
      case bw125cr46: set[0] = bw125cr46; strcat(newBWCR, "125kHz, 4_6, "); sC++; break;
      case bw125cr47: set[0] = bw125cr47; strcat(newBWCR, "125kHz, 4_7, "); sC++; break;
      case bw125cr48: set[0] = bw125cr48; strcat(newBWCR, "125kHz, 4_8, "); sC++; break;
      case bw250cr45: set[0] = bw250cr45; strcat(newBWCR, "250kHz, 4_5, "); sC++; break;
      case bw250cr46: set[0] = bw250cr46; strcat(newBWCR, "250kHz, 4_6, "); sC++; break;
      case bw250cr47: set[0] = bw250cr47; strcat(newBWCR, "250kHz, 4_7, "); sC++; break;
      case bw250cr48: set[0] = bw250cr48; strcat(newBWCR, "250kHz, 4_8, "); sC++; break;
      case bw500cr45: set[0] = bw500cr45; strcat(newBWCR, "500kHz, 4_5, "); sC++; break;
      case bw500cr46: set[0] = bw500cr46; strcat(newBWCR, "500kHz, 4_6, "); sC++; break;
      case bw500cr47: set[0] = bw500cr47; strcat(newBWCR, "500kHz, 4_7, "); sC++; break;
      case bw500cr48: set[0] = bw500cr48; strcat(newBWCR, "500kHz, 4_8, "); sC++; break;
    }
    switch (keyfromstring(token, 2)) {
      case -1: break;
      case sf128: set[1] = sf128; strcat(newSF, "128\0"); sC++; break;
      case sf256: set[1] = sf256; strcat(newSF, "256\0"); sC++; break;
      case sf512: set[1] = sf512; strcat(newSF, "512\0"); sC++; break;
      case sf1024: set[1] = sf1024; strcat(newSF, "1024\0"); sC++; break;
      case sf2048: set[1] = sf2048; strcat(newSF, "2048\0"); sC++; break;
      case sf4096: set[1] = sf4096; strcat(newSF, "4096\0"); sC++; break;
    }
    token = strtok(NULL, " ");
  }

  int c = 0;
  debug_print("Set[0 - 2] = ");
  while (c < 3) {
    debug_print(set[c]);
    c++;
  }
  if (sC < 2) {
    debug_print("That didn't work.");
    debug_print("Try again with the settings format -changemode bw___cr__ sf___");
    return -1;
  }
  char confirmation[numChars] = "";
  strcat(confirmation, "-received- New settings: ");
  strcat(confirmation, newBWCR);
  strcat(confirmation, newSF);
  debug_print(confirmation);
  delay(100);
  if (!rf95.sendtoWait((uint8_t *)confirmation, strlen(confirmation) + 1, REMOTE_ADDRESS)) {
    debug_print("No Ack received, cannot change mode.");
    return -1;
  }
  else {
    debug_print("Acknowledge received. Changing mode now.");

    RH_RF95::ModemConfig new_modem_config = {
      set[0],
      set[1],
      0x0C  // LEAVE THIS ALONE
    };
    delay(10);
    driver.setModemRegisters(&new_modem_config);      // give it the configuration we specified
    delay(10);
    if (db) {
      driver.printRegisters();
    }
  }
  return 0;
}
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
void loop()
{
  bool remoteControl = false;

  if (hsp.available() > 0) {
    digitalWrite(LED, HIGH);
    receiveLine();
    transmitLine();
    digitalWrite(LED, LOW);
  }

  if (hsp.available() == 0)
  {
    if (!SHORE) {
      if (millis() - timer > 30000) {
        battCheck();            // check the power supply if it's been more than 30 seconds
      }
    }
    // Should be a message for us now
    uint8_t buf[numChars];
    uint8_t len = sizeof(buf);
    uint8_t from;

    if (rf95.available()) {
      if (rf95.recvfromAck(buf, &len, &from)) {
        if (SHORE) {          // if shore client, give rf link info and packet time as well as message
          ledFlash(2);
          hsp.println((char*)buf);
          if (OUTMON) {
            hsp.print("RSSI: ");
            hsp.println(driver.lastRssi(), DEC);
            hsp.print("SNR: ");
            hsp.println(driver.lastSNR(), DEC);
          }
          if (MEMMON) {
            int freeMem = freeMemory();
            memDiff = lastMem - freeMem;
            lastMem = freeMem;
            hsp.print("Memory used since last receive: ");
            hsp.println(memDiff);
            hsp.print("Total memory left: ");
            hsp.println(freeMem);
            memPct = ((freeMem / 262144.0) * 100.0);
            hsp.print(memPct); hsp.println("% memory left");
          }
        }
        char tmp[numChars];
        for (int i = 0; i < numChars; i++) {
          tmp[i] = (char)buf[i];
        }
        char *token = strtok(tmp, "\n");
        token = strtok(token, " ");

        while (token != NULL) {

          if (strcmp(token, MODE) == 0) {
            remoteControl = true;
            debug_print("Request to change settings.");
            if (modeChangeRemote(buf) == 0) {
              debug_print("Transmission settings changed successfully.");
            }
          }
          else if (strcmp(token, "PING\0") == 0) {
            remoteControl = true;
            char msg[] = "pingback\0";
            transmit((uint8_t*)msg, strlen(msg));
          }
          else if (strcmp(token, RCVD) == 0) {
            remoteControl = true;
            RH_RF95::ModemConfig new_modem_config = {
              set[0],
              set[1],
              0x0C  // LEAVE THIS ALONE
            };
            delay(100);
            driver.setModemRegisters(&new_modem_config);      // give it the configuration we specified
            delay(100);
            if (db) {
              driver.printRegisters();
            }
            debug_print("confirmed. Mode has been changed to new settings.");
          }
          token = strtok(NULL, " ");
        }
        if (!remoteControl) {
          if (!SHORE) {               // if at sea, convey message verbatim
            if (from == REMOTE_ADDRESS) {     // but only if it's from us
              hsp.println((char*)buf);
            }
          }
        }

      }
    }
  }
}

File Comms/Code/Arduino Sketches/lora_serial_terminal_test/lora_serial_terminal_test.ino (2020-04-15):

// This sketch is a proof of concept to verify packet transmission of UART data
// from one LoRa radio to another. It pings out serial input to a radio to a pingback
// program and reports the packet that it receives in response.
// Currently under construction to add the ability to send command to change transmit
// settings for datarate

#include <SPI.h>
#include <RH_RF95.h>
#include <avr/dtostrf.h>
#include <RHReliableDatagram.h>


//------------------------DEBUG DEFINITIONS---------------------------------------------

#define DEBUG


// choose which hardware serial port by toggling debug mode
#ifdef DEBUG
auto hsp = Serial; // use USB serial in debug
#define debug_print(x) hsp.println(x); // provide method for tracing errors
#define debug_hold() while(!hsp){delay(1);};
#else
auto hsp = Serial1; // normal operation use UART
#endif

//-------------------------PIN DEFINITIONS------------------------------------------------

// For battery check, USB power check.
#define VBATPIN A7 // pin D9 on feather board
#define USB_PRESENT A2
#define USB_VOLTAGE 2.2   // half of maximum battery voltage. if USB pwr is gone
// the USB pin will read vBatt instead of 4.6-5.5.


// for feather m0
#define RFM95_CS 8
#define RFM95_RST 4
#define RFM95_INT 3

/* for shield
  #define RFM95_CS 10
  #define RFM95_RST 9
  #define RFM95_INT 7
*/

/* Feather m0 w/wing
  #define RFM95_RST     11   // "A"
  #define RFM95_CS      10   // "B"
  #define RFM95_INT     6    // "D"
*/

//--------------------------LORA SETTINGS DEFS---------------------------------------------

// Change to 434.0 or other frequency, must match RX's freq!
#define RF95_FREQ 915.0
#define TIMEOUT 4000
#define RETRIES 5
#define SERVER_ADDRESS 1            // AUV radio is the server
#define CLIENT_ADDRESS 2            // shore pc is the client

// Singleton instance of the radio driver
RH_RF95 driver(RFM95_CS, RFM95_INT);                // driver is radio hardware driver
RHReliableDatagram rf95(driver,SERVER_ADDRESS);     // rf95 is the msg manager

//--------------------------Ping Time Variables--------------------------------------------


unsigned long lastMsg;
unsigned long timeSince;
unsigned long longestBreak = 0;
int longestMin = 0;
int longestSec = 0;
int seconds;
int minutes;

void setup()
{
  lastMsg = millis();
  pinMode(RFM95_RST, OUTPUT);
  digitalWrite(RFM95_RST, HIGH);

  pinMode(USB_PRESENT, INPUT);      // check to see if USB power is present
  pinMode(VBATPIN, INPUT);          // monitor battery level

  hsp.begin(9600);  // hsp = hardware serial port. usb in debug mode, uart in prod. mode.
  debug_hold();
  delay(100);
  hsp.println("Feather LoRa TX Test!");

  // manual reset
  digitalWrite(RFM95_RST, LOW);
  delay(10);
  digitalWrite(RFM95_RST, HIGH);
  delay(10);

  //----------------------RFM95 Configuration Time-----------------------------------------

  while (!rf95.init()) {
    hsp.println("LoRa radio init failed");
    hsp.println("Uncomment '#define SERIAL_DEBUG' in RH_RF95.cpp for detailed debug info");
    while (1);
  }
  hsp.println("LoRa radio init OK!");

  // Defaults after init are 434.0MHz, modulation GFSK_Rb250Fd250, +13dbM
  if (!driver.setFrequency(RF95_FREQ)) {
    hsp.println("setFrequency failed");
    while (1);
  }
  
  hsp.print("Set Freq to: "); hsp.println(RF95_FREQ);

  // Defaults after init are 434.0MHz, 13dBm, Bw = 125 kHz, Cr = 4/5, Sf = 128chips/symbol, CRC on
  // Change this to taste by editing modem_config below:

  RH_RF95::ModemConfig modem_config = {
    0x72, // Reg 0x1D: BW=125kHz, Coding=4/8, Header=explicit... bits 7-4 govern BW, 3-1 governs C.R.
    // LSB is header mode, leave as zero. 0x_2, 0x_4, 0x_6, 0x_8 represent C.R from 4/5->4/8.
    // All other values of bits 3-0 reserved. Useable BW ranges from 0x5_ (31.25kHz) to 0x9_ (500kHz).
    0x84, // Reg 0x1E: Spread=512chips/symbol, CRC=enable...each bit increase in first nibble
    // of the byte corresponds to doubling of spreading factor (change 0x94 to 0xC4 for max)
    // Don't change bits 3-0.
    0x0C  // Reg 0x26: LowDataRate=On, Agc=On... only bits 3 and 2 have meaning. bit 3 = mobile node?
    // bit 2 = automatic AGC?
  };

  driver.setModemRegisters(&modem_config);      // give it the configuration we specified
  driver.setTxPower(23, false);                 // don't touch this. max output power, no PA_BOOST pin avail.
  rf95.setRetries(RETRIES);
  rf95.setTimeout(TIMEOUT);
}

//------------------Serial Input Methods---------------------------------------------

// set vars for serial input function
const byte numChars = 255;  // limits read to 255 bytes (full size of serial buffer
                            // and max length of a lora payload)
char msgBuffer[numChars];
boolean newData = false;
int packetSize;
int timeSent = 0;

void receiveLine() {
  static byte ndx = 0;
  char endMarker = '\n';
  char rc;
  while (hsp.available() > 0) {
    rc = hsp.read();

// -----------------------NEED ERROR CORRECTION IF INPUT > 253 CHARS-------------
    
    if ((rc != endMarker) && (ndx < (numChars - 2))) {
      msgBuffer[ndx] = rc;
      ndx++;
      if (ndx >= numChars) {
        ndx = numChars - 1;
      }
    }
    else {
      msgBuffer[ndx] = '\n';
      ndx++;
      msgBuffer[ndx] = '\0';
      ndx = 0;
      newData = true;
    }
  }
}

//----------------------LoRa methods---------------------------------------------

void transmit(char msg[], int msgLength){
  if (!rf95.sendtoWait((uint8_t *)msg, msgLength+1, 1)){
    hsp.println("Transmission failed. No ACK received.");
  }
  else{
    hsp.println("Transmission successful.");
  }
}

void transmitLine() {
  if (newData == true) {
    hsp.println(msgBuffer);
    newData = false;
    hsp.println("Transmitting...");             // Send a message to rf95_server
    transmit(msgBuffer, strlen(msgBuffer));  //send() needs uint8_t so we cast it
    timeSent = millis();
  }
}

void battLevel() {
  float vBatt = analogRead(VBATPIN);
  vBatt *= 2;           // undo voltage divider
  vBatt *= 3.3;         // full scale reference
  vBatt /= 1023;        // undo analogRead() 10bit integer scaling
  char cBuff[20];
  sprintf(cBuff, "%6.3f", vBatt); // cast voltage as c style string
  char voltagePacket[] = "";
  strcat(voltagePacket, "Current battery voltage: ");
  strcat(voltagePacket, cBuff);
  transmit(voltagePacket, strlen(voltagePacket));
}



void battCheck() {
  float cmpVoltage = analogRead(USB_PRESENT);
  cmpVoltage *= 3.3;
  cmpVoltage /= 1023;
  if (cmpVoltage < USB_VOLTAGE) {
    char helpMsg[numChars] = "";
    strcat(helpMsg, "The power system has failed. Please come find me. I'm scared.");
    transmit(helpMsg, strlen(helpMsg));
    battLevel();
    delay(30000);       // wait 30 seconds
  }
}

//--------------------------------Mainline-----------------------------------
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

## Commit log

2020-03-13 prepare the soil bed for planting of code.
    [project.cfg]
2020-03-27 Sonar code
2020-03-31 Skeleton of UART process daemon
2020-04-02 Cleaned up the Payload Power Board sch and brd and am almost done with the Voltage Lines Board sch and brd
    [march_23_20_power_board1_v2.0.brd, march_23_20_power_board1_v2.0.sch, power_board2_v1.0.brd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]
2020-04-08 Included larger size mounting holes on both .brd files, pretty much finished board 2 (haven't GND'ed yet, need a design review)
    [power_board1_v2.0.brd, power_board2_v2.0.brd, power_board2_v2.0.sch]
2020-04-08 cleaned arduino sketches, still in progress
2020-04-09 fixed bug which was adding unprintable characters to some serial input
    [LoRa_test_Rx.ino, lora_serial_terminal_test.ino]
2020-04-11 power system failure broadcast code module tested and integrated
    [lora_serial_terminal_test.ino]
2020-04-11 prevented buffer size problems I hope
    [LoRa_test_Rx.ino, lora_serial_terminal_test.ino]
2020-04-15 Redesigned layout to fit in AUV. Changed 18V and 24V to mini and micro (also vertical), tucked connectors into board, all wrapped up
    [power_board1_v2.0.brd, power_board1_v2.0.sch]
2020-04-15 Forgot to add names to components (helpful for assembly)
    [power_board1_v2.0.brd, power_board1_v2.0.sch]
2020-04-23 added packet timer, cleaned and consolidated code a bit.
2020-04-27 Boards being made at OSHPark were wrt these files
    [power_board1_v2.0.brd, power_board1_v2.0.sch]
2020-04-29 Rename Sonar/.gitkeep3 to Sonar/Linux Code/.gitkeep3
2020-04-29 Rename Sonar/Makefile to Sonar/Linux Code/Makefile
2020-04-30 finished Arduino sketches pending reorganizing them for clarity
2020-05-01 added some fine tuning to arduino code to enable handshake-free settings change
2020-05-17 python UART daemon, some touchup on arduino code
2020-05-18 fixed -changemode method, made backspace-safe
    [pyTerminal.py]
2020-05-24 Improved documentation on these two files
    [Payload_Power_Board.brd, Payload_Power_Board.sch]
2020-06-01 delete README.md
    Refer to the Sonar Software Manual on how to execute the program
2020-06-04 Updated the expected input voltage range
    [Payload_Power_Board.sch]
2020-11-12 Post Processing
    Created a folder for post processing and a inserted a livescript for processing alog files.
2020-12-11 Description updates
    Nothing special
    [MayfieldBridgeAgain5.872.AlternateData.csv]
2020-12-30 Cleanup
    Excludes superfluous data restricted to sample data and outputs.
    [MOOSLog_8_11_2020_____23_32_45_alvtmp.csv, MayfieldBridgeAgain5.872.AlternateData.csv, SonarTRX_Sample_Output.csv]
2020-12-30 Alexs parser
    Includes Alex Higgen's parser and some sample data
2021-03-05 Post Processing is now Operations
    It's been a while since I've updated, but the matlab script has changed a little to be more robust and to include a plot that once perfected will have lat/long, depth, desired depth, and altitude.
    [MOOSLog_8_11_2020_____23_32_45_alvtmp.csv, SonarTRX_Sample_Output.csv]
2021-03-05 Small changes to alogProcessor
    [MOOSLog_3_3_2021_____00_06_40.csv]
2021-03-05 small updates and sample files
    [MOOSLog_3_3_2021_____00_06_40.csv, MOOSLog_3_3_2021_____00_21_43.csv, MOOSLog_3_3_2021_____00_35_18.csv]
2021-03-09 small inline description updates
    [MOOSLog_3_3_2021_____00_06_40.csv, MOOSLog_3_3_2021_____00_21_43.csv, MOOSLog_3_3_2021_____00_35_18.csv]
2021-05-21 Folder structure
    It's nothing really.
    [SonarTRX_Sample_Output.csv]
